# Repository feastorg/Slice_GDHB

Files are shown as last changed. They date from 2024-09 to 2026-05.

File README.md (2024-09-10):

# Gate-Driven H-Bridge Slice

Gate-driven Discrete H-Bridge Slice for BREAD.

## Introduction

[Short introduction on the project.]

## Usage

[Explain how to use the project. Include examples and screenshots if applicable.]

## Documentation

Please refer to the [docs](/docs) for more info.

---

<div align="center">
  <p>
    
    
  </p>
</div>

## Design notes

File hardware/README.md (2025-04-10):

# Hardware Notes

- Driver A4957SESTR-T
  - https://www.digikey.ca/en/products/detail/allegro-microsystems/A4957SESTR-T/3770630
- wago terminal block:
  - https://www.digikey.ca/en/products/detail/wago-corporation/2606-1104-010-000/15538173
- MOSFETS
  - https://www.digikey.ca/en/products/detail/nexperia-usa-inc/PSMN1R0-30YLC-115/2674282
-

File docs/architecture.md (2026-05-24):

---
title: "Architecture"
description: "Hardware and firmware architecture overview."
---

# Architecture

## Hardware

Gate Driver H-Bridge (GDHB) motor control slice (4-layer PCB). Uses A4957 dual full-bridge gate driver.

## Firmware

_Not yet developed._

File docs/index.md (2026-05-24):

---
title: "Slice GDHB Documentation"
description: "Overview and entry page for Slice GDHB project documentation."
nav_exclude: true
---

Welcome to the Slice GDHB project documentation.

## Board Renders

<figure style="display:inline-block; text-align:center; margin:10px;">
  Board Top
  <figcaption>Top</figcaption>
</figure>

<figure style="display:inline-block; text-align:center; margin:10px;">
  Board Bottom
  <figcaption>Bottom</figcaption>
</figure>

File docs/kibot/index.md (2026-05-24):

---
title: "KiBot Outputs"
description: "Index for KiBot-generated PCB artifacts."
layout: "page"
---

These are the docs & KiBot Outputs for Slice GDHB

The following files were generated from the latest PCB build:

_(Not yet generated — will be populated by CI on first successful run.)_

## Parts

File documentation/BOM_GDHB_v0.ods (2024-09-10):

Reference | Value | Datasheet | Footprint | Qty | Unit Cost | Cost | URL
A1 | Arduino_Nano_v3.x | http://www.mouser.com/pdfdocs/Gravitech_Arduino_Nano3_0.pdf | Module:Arduino_Nano | 1 | $10.00 | $10.00
C1,C3,C4 | 22uF | ~ | Capacitor_SMD:C_1206_3216Metric | 3 | $0.20 | $0.60 | https://www.digikey.ca/en/products/detail/samsung-electro-mechanics/CL31A226KAHNNNE/3888705
C2 | 100nF | ~ | Capacitor_SMD:C_1206_3216Metric | 1 | $0.20 | $0.20 | https://www.digikey.ca/en/products/detail/samsung-electro-mechanics/CL31B104KBCNNNC/3886675
C6,C13 | 100nF | ~ | Capacitor_SMD:C_0805_2012Metric | 2 | $0.20 | $0.40
C5,C12 | 10uF | ~ | Capacitor_SMD:C_0805_2012Metric | 2 | $0.20 | $0.40
C7,C8,C14,C15 | 50V 220uF | ~ | Capacitor_SMD:CP_Elec_10x10 | 4 | $0.20 | $0.80
C9,C10,C16,C17 | 1nF | ~ | Capacitor_SMD:C_0805_2012Metric | 4 | $0.20 | $0.80
C11,C18 | 50V 10uF | ~ | Capacitor_SMD:C_0805_2012Metric | 2 | $0.20 | $0.40
Cp1,Cp2 | 16V 470nF | ~ | Capacitor_SMD:C_0805_2012Metric | 2 | $0.20 | $0.40
Creg1,Creg2 | 16V 22uF | ~ | Capacitor_SMD:C_0805_2012Metric | 2 | $0.20 | $0.40
D1 | WS2812B_5050 | https://cdn.sparkfun.com/datasheets/BreakoutBoards/WS2812B.pdf | SparkFun-LED:WS2812-5050-4PIN | 1 | $0.92 | $0.92
H1,H2,H3,H4 | MountingHole | ~ | MountingHole:MountingHole_5mm | 4 | $0.00 | $0.00
HS1 | Heatsink_Pad | ~ | KML-Custom:Thermal Pad | 1 | $0.85 | $0.85 | https://www.digikey.ca/en/products/detail/assmann-wsw-components/V2017B/3511410
J1 | I2C_01x04 | ~ | Connector_JST:JST_SH_SM04B-SRSS-TB_1x04-1MP_P1.00mm_Horizontal | 1 | $0.97 | $0.97 | https://www.digikey.ca/en/products/detail/sullins-connector-solutions/PPTC101LGBN-RC/775904
J2 | Conn_01x10_Female | ~ | Connector_PinSocket_2.54mm:PinSocket_1x10_P2.54mm_Horizontal | 1 | $1.11 | $1.11 | https://www.digikey.ca/en/products/detail/jst-sales-america-inc/SM04B-SRSS-TB/926710
J3,J4,J5,J6 | Conn_01x02_Socket | ~ | Library:Term_Block_1x2_P10.16mm | 4 | $3.76 | $15.04 | https://www.digikey.ca/en/products/detail/amphenol-anytek/VP0265540000G/4957847
JP1,JP2 | Jumper_2_Open | ~ | Capacitor_SMD:C_0805_2012Metric | 2 | $0.20 | $0.40
L1 | 4.7uH | ~ | Inductor_SMD:L_1210_3225Metric | 1 | $2.37 | $2.37 | https://www.digikey.ca/en/products/detail/tdk-corporation/BCL322520RT-4R7M-D/15849704
Q1,Q2,Q3,Q4,Q5,Q6,Q7,Q8 | PSMN1R0-30YLC,115 | https://assets.nexperia.com/documents/data-sheet/PSMN1R0-30YLC.pdf | Package_TO_SOT_SMD:LFPAK56 | 8 | $3.01 | $24.08 | https://www.digikey.ca/en/products/detail/nexperia-usa-inc/PSMN1R0-30YLC-115/2674282
R1,R6,R7,R12 | 10K | ~ | Capacitor_SMD:C_0805_2012Metric | 4 | $0.20 | $0.80
R2,R3,R4,R5,R8,R9,R10,R11 | 1K | ~ | Capacitor_SMD:C_0805_2012Metric | 8 | $0.20 | $1.60
U1 | IC REG BUCK 5V 2A TSOT23-6 |  | TSOT-23-6 | 1 | $1.34 | $1.34 | https://www.digikey.ca/en/products/detail/diodes-incorporated/AP63205WU-7/9858424
U2, U3 | A4957 |  | Package_DFN_QFN:HVQFN-24-1EP_4x4mm_P0.5mm_EP2.6x2.6mm_ThermalVias | 2 | $3.10 | $6.20 | https://www.digikey.ca/en/products/detail/allegro-microsystems/A4957SESTR-T/3770630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
 |  |  | PCB | 1 | $5.00 | $5.00
 |  |  |  |  |  | $75.08
 |  |  |  |  |  | $84.84

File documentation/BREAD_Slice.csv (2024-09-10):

Reference | Value | Datasheet | Footprint | Qty | DNP
A1 | Arduino_Nano_v3.x | http://www.mouser.com/pdfdocs/Gravitech_Arduino_Nano3_0.pdf | Module:Arduino_Nano | 1
C1,C3,C4 | 22uF | ~ | Capacitor_SMD:C_1206_3216Metric | 3
C2,C6,C13 | 100nF | ~ | -- mixed values -- | 3
C5,C12 | 10uF | ~ | Capacitor_SMD:C_0805_2012Metric | 2
C7,C8,C14,C15 | 50V 220uF | ~ | Capacitor_SMD:CP_Elec_10x10 | 4
C9,C10,C16,C17 | 1nF | ~ | Capacitor_SMD:C_0805_2012Metric | 4
C11,C18 | 50V 10uF | ~ | Capacitor_SMD:C_0805_2012Metric | 2
Cp1,Cp2 | 16V 470nF | ~ | Capacitor_SMD:C_0805_2012Metric | 2
Creg1,Creg2 | 16V 22uF | ~ | Capacitor_SMD:C_0805_2012Metric | 2
D1 | WS2812B_5050 | https://cdn.sparkfun.com/datasheets/BreakoutBoards/WS2812B.pdf | SparkFun-LED:WS2812-5050-4PIN | 1
H1,H2,H3,H4 | MountingHole | ~ | MountingHole:MountingHole_5mm | 4
HS1 | Heatsink_Pad | ~ | KML-Custom:Thermal Pad | 1
J1 | I2C_01x04 | ~ | Connector_JST:JST_SH_SM04B-SRSS-TB_1x04-1MP_P1.00mm_Horizontal | 1
J2 | Conn_01x10_Female | ~ | Connector_PinSocket_2.54mm:PinSocket_1x10_P2.54mm_Horizontal | 1
J3,J4,J5,J6 | Conn_01x02_Socket | ~ | Library:Term_Block_1x2_P10.16mm | 4
JP1,JP2 | Jumper_2_Open | ~ | Capacitor_SMD:C_0805_2012Metric | 2
L1 | 4.7uH | ~ | Inductor_SMD:L_1210_3225Metric | 1
Q1,Q2,Q3,Q4,Q5,Q6,Q7,Q8 | PSMN1R0-30YLC,115 | https://assets.nexperia.com/documents/data-sheet/PSMN1R0-30YLC.pdf | Package_TO_SOT_SMD:LFPAK56 | 8
R1,R6,R7,R12 | 10K | ~ | Capacitor_SMD:C_0805_2012Metric | 4
R2,R3,R4,R5,R8,R9,R10,R11 | 1K | ~ | Capacitor_SMD:C_0805_2012Metric | 8
U1,U2,U3 | ~ |  | -- mixed values -- | 3

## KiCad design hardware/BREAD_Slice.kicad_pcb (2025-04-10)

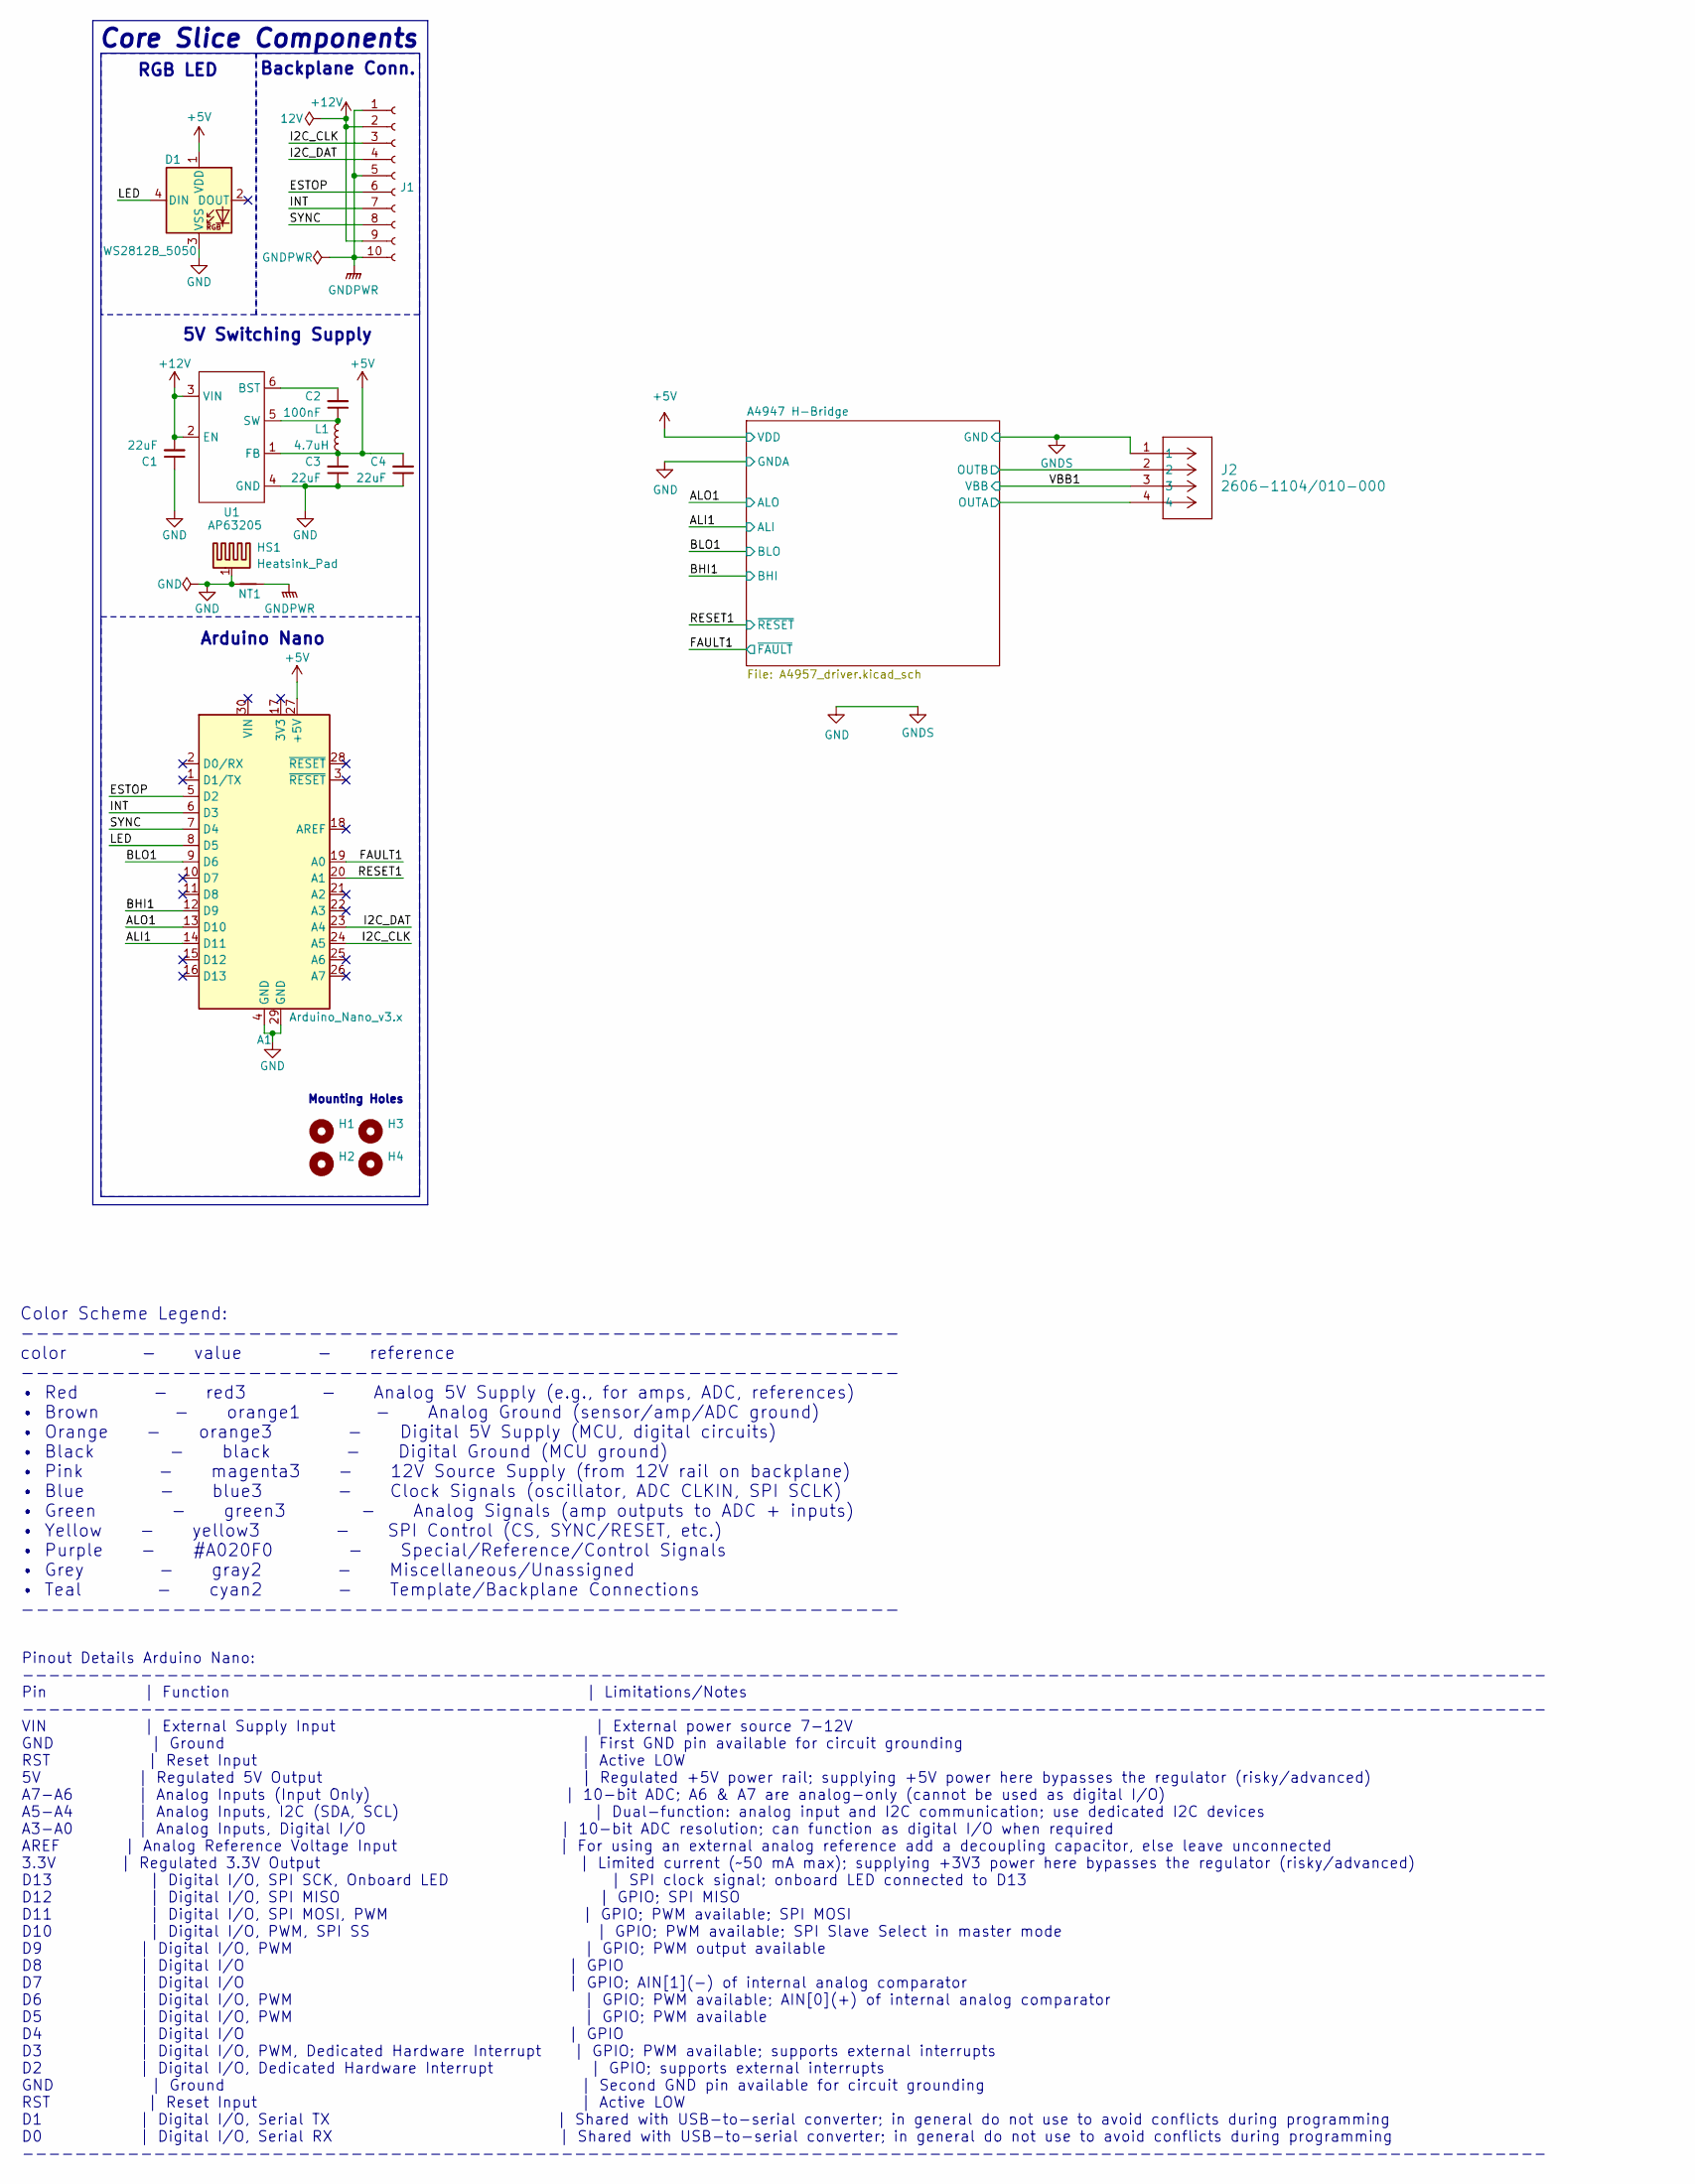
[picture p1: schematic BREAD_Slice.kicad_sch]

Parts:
A1: Arduino_Nano_v3.x; Arduino_Nano
C1, C3, C4: 22uF; C_1206_3216Metric_Pad1.33x1.80mm_HandSolder
C2: 100nF; C_1206_3216Metric_Pad1.33x1.80mm_HandSolder
D1: WS2812B_5050; WS2812-5050-4PIN
H1, H2, H3, H4: MountingHole; MountingHole_5mm
HS1: Heatsink_Pad; Thermal Pad
J1: Conn_01x10_Female; PinSocket_1x10_P2.54mm_Horizontal
J2: 2606-1104/010-000; CONN4_2606-1104&slash_010-000_WAG
L1: 4.7uH; L_1210_3225Metric
NT1: NetTie_2; NetTie-2_SMD_Pad2.0mm
U1: AP63205; TSOT-23-6

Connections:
+5V: A1.27 (+5V), C3.2, C4.2, D1.1 (VDD), L1.2, U1.1 (FB); also elsewhere on the board
+12V: C1.2, J1.2, J1.9, U1.2 (EN), U1.3 (VIN)
/A4947 H-Bridge/SA: J2.4; also elsewhere on the board
/A4947 H-Bridge/SB: J2.2; also elsewhere on the board
/ALI1: A1.14 (D11); also elsewhere on the board
/ALO1: A1.13 (D10); also elsewhere on the board
/BHI1: A1.12 (D9); also elsewhere on the board
/BLO1: A1.9 (D6); also elsewhere on the board
/ESTOP: A1.5 (D2), J1.6
/FAULT1: A1.19 (A0); also elsewhere on the board
/I2C_CLK: A1.24 (A5), J1.3
/I2C_DAT: A1.23 (A4), J1.4
/INT: A1.6 (D3), J1.7
/LED: A1.8 (D5), D1.4 (DIN)
/RESET1: A1.20 (A1); also elsewhere on the board
/SYNC: A1.7 (D4), J1.8
/VBB1: J2.3; also elsewhere on the board
GND: A1.4 (GND), A1.29 (GND), C1.1, C3.1, C4.1, D1.3 (VSS), HS1.1, J2.1, NT1.1, U1.4 (GND); also elsewhere on the board
GNDPWR: J1.1, J1.5, J1.10, NT1.2
unnamed: C2.2, U1.6 (BST)
unnamed: C2.1, L1.1, U1.5 (SW)

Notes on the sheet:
5V Switching Supply
Pinout Details Arduino Nano: -------------------------------------------------------------------------------------------------------------------- Pin | Function | Limitations/Notes -------------------------------------------------------------------------------------------------------------------- V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
RGB LED
Color Scheme Legend: ---------------------------------------------------------- color - value - reference ---------------------------------------------------------- • Red - red3 - Analog 5V Supply (e.g., for amps, ADC, references) • Brown - orange1 - Analog Ground (sensor/amp/ADC ground) • Orange -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
Core Slice Components
Arduino Nano
Mounting Holes
Backplane Conn.

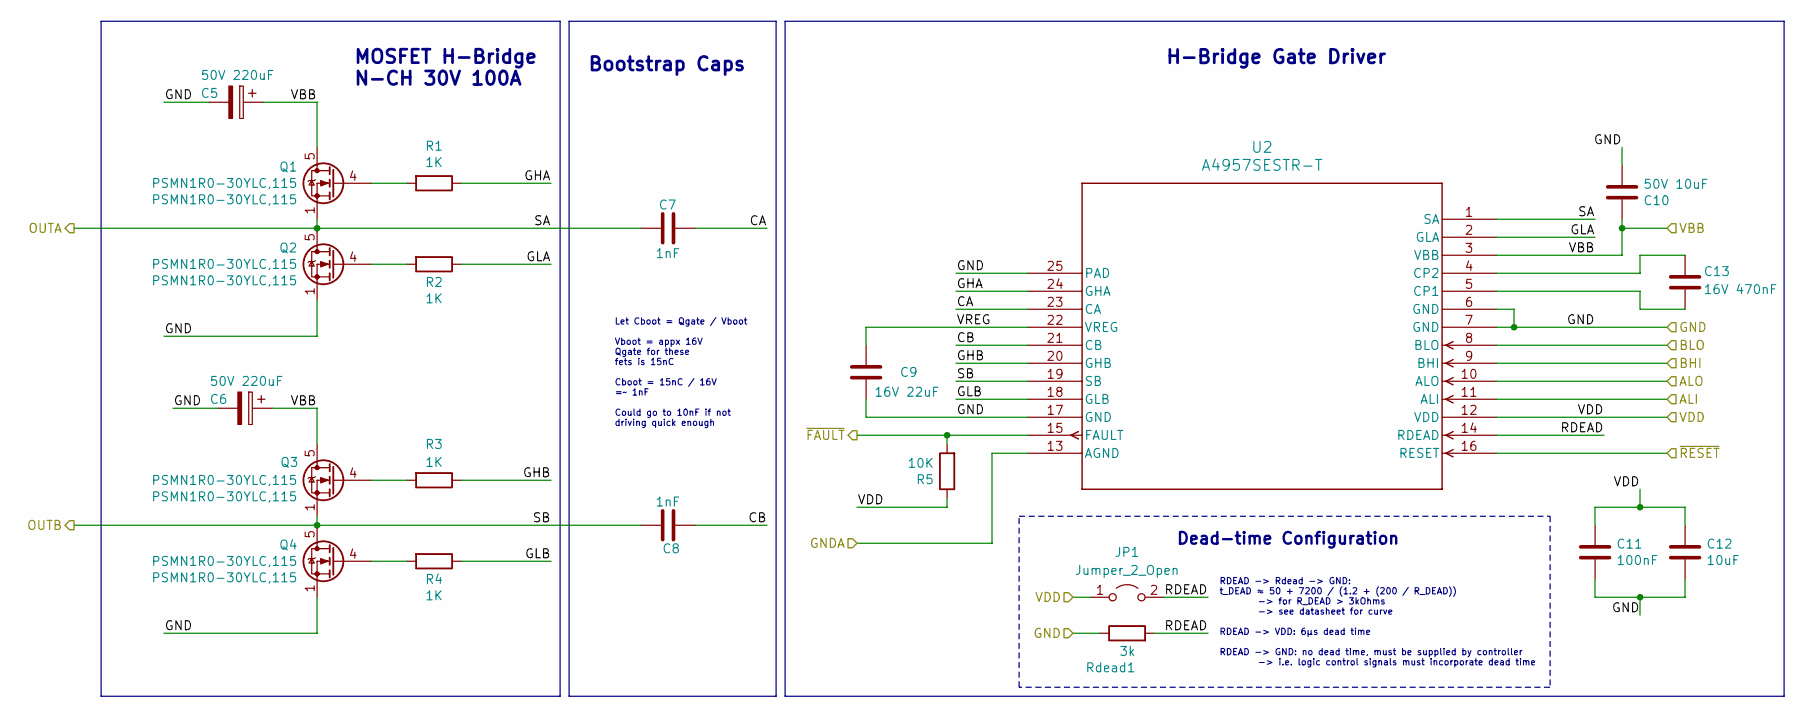
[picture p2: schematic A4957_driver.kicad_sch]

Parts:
C5, C6: 50V 220uF; CP_Elec_10x10
C7, C8: 1nF; C_0805_2012Metric_Pad1.18x1.45mm_HandSolder
C9: 16V 22uF; C_0805_2012Metric_Pad1.18x1.45mm_HandSolder
C10: 50V 10uF; C_0805_2012Metric_Pad1.18x1.45mm_HandSolder
C11: 100nF; C_0805_2012Metric_Pad1.18x1.45mm_HandSolder
C12: 10uF; C_0805_2012Metric_Pad1.18x1.45mm_HandSolder
C13: 16V 470nF; C_0805_2012Metric_Pad1.18x1.45mm_HandSolder
JP1: Jumper_2_Open; C_0805_2012Metric
Q1, Q2, Q3, Q4: PSMN1R0-30YLC,115; LFPAK56; MPN PSMN1R0-30YLC,115
R1, R2, R3, R4: 1K; R_0805_2012Metric_Pad1.20x1.40mm_HandSolder
R5: 10K; R_0805_2012Metric_Pad1.20x1.40mm_HandSolder
Rdead1: 3k; R_0805_2012Metric_Pad1.20x1.40mm_HandSolder
U2: A4957SESTR-T; QFN-24_ALM

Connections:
+5V: C11.1, C12.1, JP1.1 (A), R5.1, U2.12 (VDD); also elsewhere on the board
/A4947 H-Bridge/CA: C7.2, U2.23 (CA)
/A4947 H-Bridge/CB: C8.2, U2.21 (CB)
/A4947 H-Bridge/GHA: R1.1, U2.24 (GHA)
/A4947 H-Bridge/GHB: R3.1, U2.20 (GHB)
/A4947 H-Bridge/GLA: R2.1, U2.2 (GLA)
/A4947 H-Bridge/GLB: R4.1, U2.18 (GLB)
/A4947 H-Bridge/RDEAD: JP1.2 (B), Rdead1.2, U2.14 (RDEAD)
/A4947 H-Bridge/SA: C7.1, Q1.1 (S), Q1.2 (S), Q1.3 (S), Q2.5 (D), U2.1 (SA); also elsewhere on the board
/A4947 H-Bridge/SB: C8.1, Q3.1 (S), Q3.2 (S), Q3.3 (S), Q4.5 (D), U2.19 (SB); also elsewhere on the board
/A4947 H-Bridge/VREG: C9.1, U2.22 (VREG)
/ALI1: U2.11 (ALI); also elsewhere on the board
/ALO1: U2.10 (ALO); also elsewhere on the board
/BHI1: U2.9 (BHI); also elsewhere on the board
/BLO1: U2.8 (BLO); also elsewhere on the board
/FAULT1: R5.2, U2.15 (FAULT); also elsewhere on the board
/RESET1: U2.16 (RESET); also elsewhere on the board
/VBB1: C5.1, C6.1, C10.1, Q1.5 (D), Q3.5 (D), U2.3 (VBB); also elsewhere on the board
GND: C5.2, C6.2, C9.2, C10.2, C11.2, C12.2, Q2.1 (S), Q2.2 (S), Q2.3 (S), Q4.1 (S), Q4.2 (S), Q4.3 (S), Rdead1.1, U2.6 (GND), U2.7 (GND), U2.13 (AGND), U2.17 (GND), U2.25 (PAD); also elsewhere on the board
unnamed: Q1.4 (G), R1.2
unnamed: Q2.4 (G), R2.2
unnamed: Q3.4 (G), R3.2
unnamed: Q4.4 (G), R4.2
unnamed: C13.1, U2.5 (CP1)
unnamed: C13.2, U2.4 (CP2)

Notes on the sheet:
Dead-time Configuration
Let Cboot = Qgate / Vboot Vboot = appx 16V Qgate for these fets is 15nC Cboot = 15nC / 16V =~ 1nF Could go to 10nF if not driving quick enough
Bootstrap Caps
RDEAD -> Rdead -> GND: t_DEAD ≈ 50 + 7200 / (1.2 + (200 / R_DEAD)) -> for R_DEAD > 3kOhms -> see datasheet for curve RDEAD -> VDD: 6µs dead time RDEAD -> GND: no dead time, must be supplied by controller -> i.e. logic control signals must incorporate dead time
H-Bridge Gate Driver
MOSFET H-Bridge N-CH 30V 100A

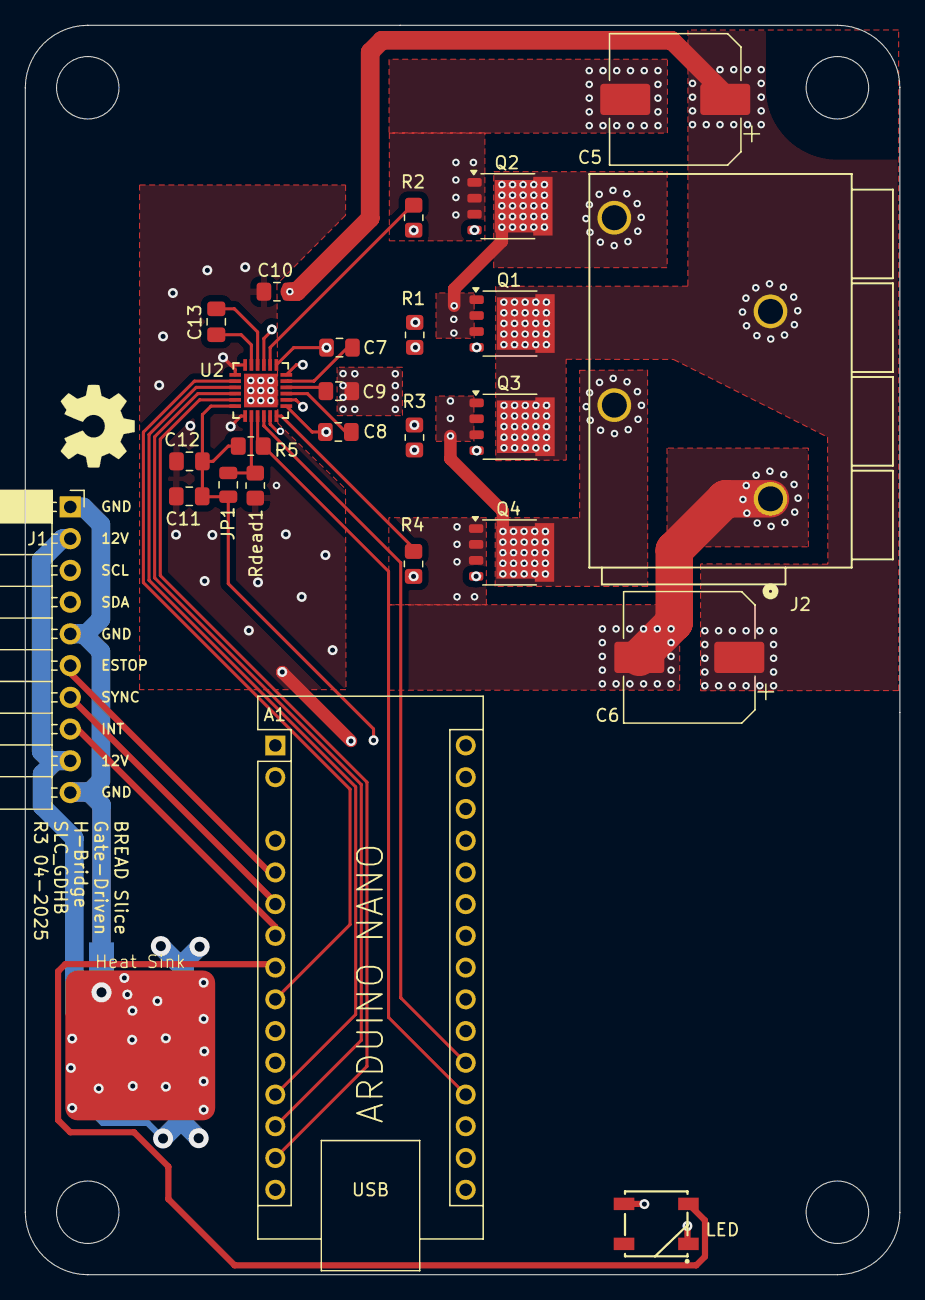
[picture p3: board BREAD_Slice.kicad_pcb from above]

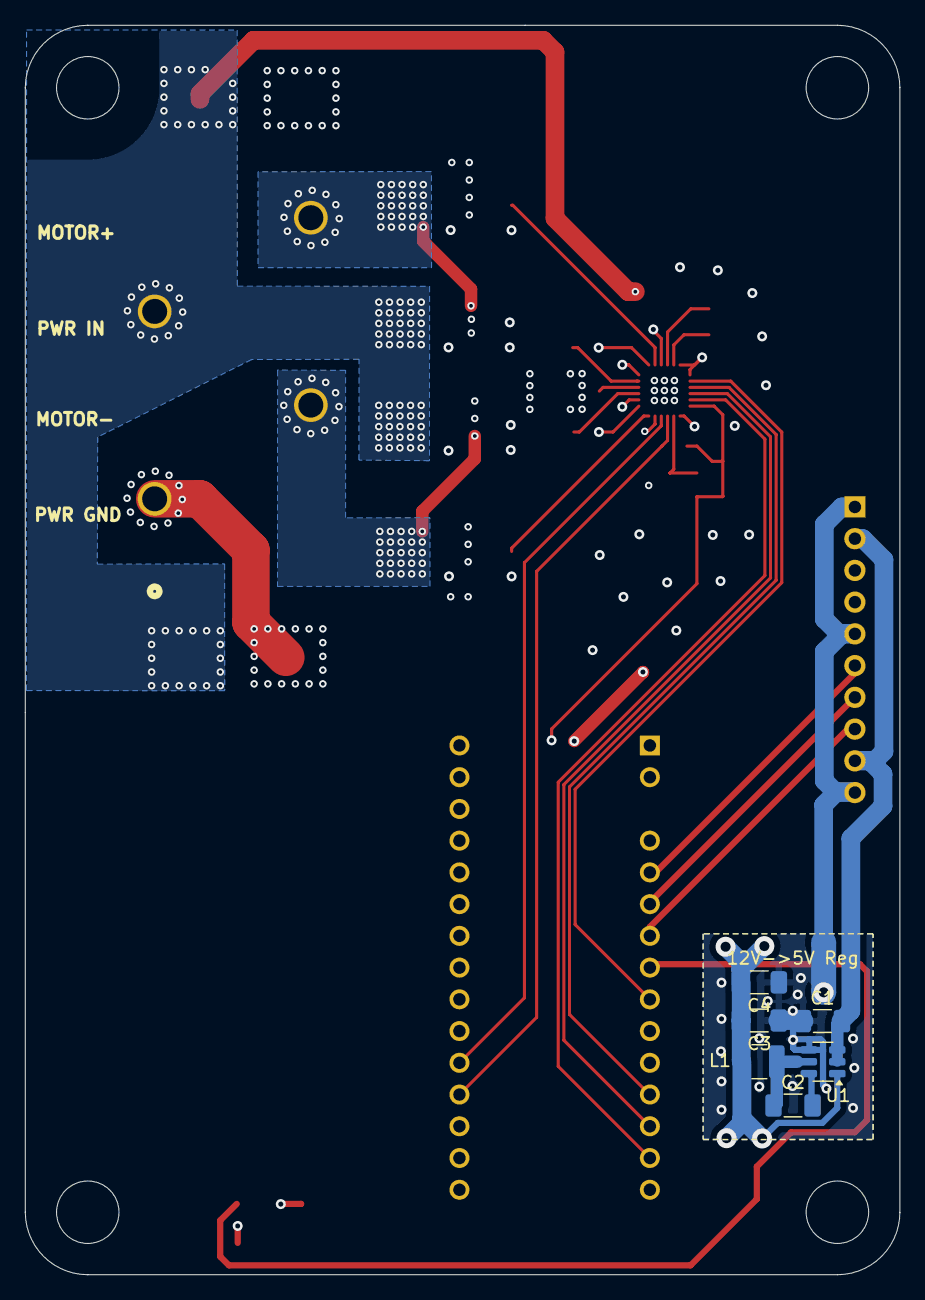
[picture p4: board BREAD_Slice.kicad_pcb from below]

Board: 4 copper layers, 70.0 x 100.0 mm, 38 parts (7 on the bottom side), 35 nets.

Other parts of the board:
Logo1: Logo_Open_Hardware_Small; OSHW-Symbol_6.7x6mm_SilkScreen

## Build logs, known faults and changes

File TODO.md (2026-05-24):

# Slice_GDHB TODO

## CI Results (Pass 1)

- [x] DRC: FAIL — 6 errors (all zones_intersect: copper zones with same priority intersecting)
- [x] ERC: FAIL — 1 error (power_pin_not_driven: input power pin not driven by any output power pins)
- [x] Fab: FAIL (blocked by ERC error)
- [ ] gen-kibot-index: SKIPPED (upstream failed)
- [ ] deploy-pages: SKIPPED (upstream failed)

**Note: 4-layer board (In1.Cu/In2.Cu enabled in kibot config)**

## Pass 2 – Pre-fab Review

- [ ] Fix 6x zone intersect errors (set distinct zone priorities)
- [ ] Fix 1x power_pin_not_driven ERC error
- [ ] Verify BOM completeness
- [ ] Confirm board outline and mounting holes
- [ ] Update README.md (still says "Slice Template")

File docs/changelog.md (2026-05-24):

---
title: "Changelog"
description: "Hardware and firmware revision history."
---

# Changelog

## Hardware

### v0.1.0 (initial)
- Initial schematic and PCB layout (4-layer)
- A4957 gate driver sub-circuit

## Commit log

2024-07-10 initial layout poisitions done
    [A4957_driver.kicad_sch, BREAD_Slice.kicad_pcb, BREAD_Slice.kicad_sch]
2024-09-10 set repo
    [A4957_driver.kicad_sch, BOM_GDHB_v0.ods, BOM_TEMP.ods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]
2025-04-10 finished initial schematic and board
    [A4957_driver.kicad_sch, BREAD_Slice.kicad_pcb, BREAD_Slice.kicad_sch]
2025-04-10 removed old
    [A4957_driver.kicad_sch, BREAD_Slice.kicad_pcb, BREAD_Slice.kicad_sch]
2026-04-18 chore: generate gerbers
    [BREAD_Slice-B_Cu.gbr, BREAD_Slice-B_Mask.gbr, BREAD_Slice-B_Paste.gbr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]
